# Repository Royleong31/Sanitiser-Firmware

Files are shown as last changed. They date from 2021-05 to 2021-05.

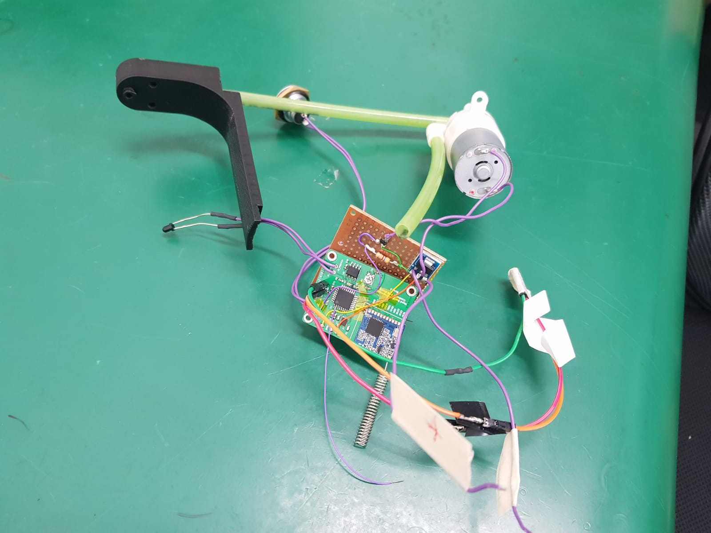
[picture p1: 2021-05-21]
Dispenser without WiFi/Dispenser/Electronics.jpeg

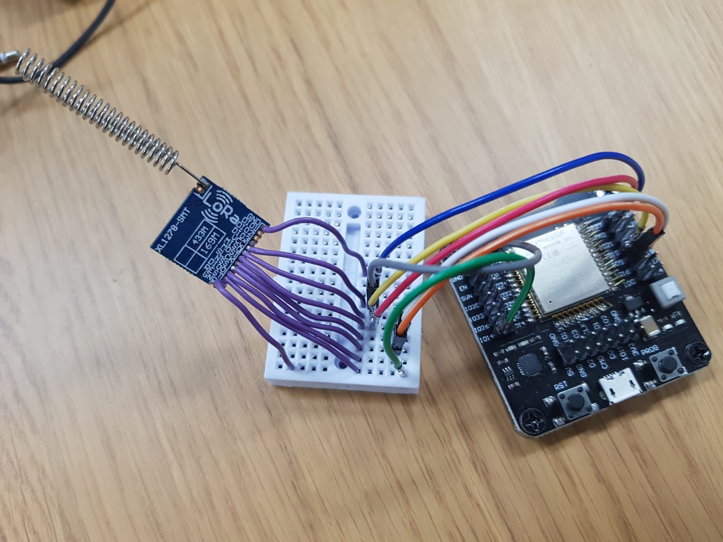
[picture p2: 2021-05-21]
Dispenser without WiFi/Gateway/Gateway Prototype.jpeg

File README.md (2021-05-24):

## General Info about Hand Sanitiser System
- The purpose is to solve the problem of cleaning staff not knowing when the refills of their hand sanitiser dispensers are running out.
- This system aims to alert the users when their dispensers are running out.
- The app will send alert notifications to users to alert them (more information about the hand sanitiser can be found in the hand sanitiser app folder README)
- The app and the firmware for the dispensers and gateway are connected by the Hand Sanitiser backend (more info can be found in that folder)
- There are 2 versions of this system: 
    1) Dispenser with WiFi (this requires the dispenser to be connected to WiFi and plugged into a power supply)
    2) Dispenser without WiFi (this requires the gateway to be connected to WiFi and power supply, but the dispenser is battery operated and does not require a WiFi connection, but not more than 50-100m away from gateway)
- The buffers in the Gateway and Dispenser with WiFi function as circular queues, with the data to be sent being queued (added to the queue). When the data is sent by the API successfully, the data is dequeued (removed from the queue)
- Queues are a form of data structure that follow the First In First Out principle

---------------------------------------------------------------------------------
Bill of materials
- Some components may need to be replaced or added
- If you have any questions regarding the electronics, you can approach Yu Jing

---------------------------------------------------------------------------------

Dispenser without WiFi
- The gateway and dispenser communicate via LoRa, a long range radio protocol.
- Packets are only sent from the dispenser to the gateway (dispenser functions as a beacon, beaming information to the gateway, but the gateway does not reply)
- There are 2 files inside this folder (Gateway and Dispenser)
- LoRa packet is a string, consisting of 3 segments of information, each separated by a space. The first segment is the companyId, second segment is the dispenserId, third is the type of usage.

1) Dispenser
    - A voltage of 3.3V-3.6V is used as that is the required voltage for the MOSFET to work properly (MOSFET is unreliable when GPIO voltage is too low).
    - The dispenser is programmed using an FTDI adapter that is connected to the RX, TX, DTR pins of the PCB. While programming the chip, the chip needs to be powered by the 3.3V and ground of the FTDI.
    
    ~ Electronics
    - Uses a custom PCB with ATMEGA328P chip, runs on 4 AA batteries
    - The input voltage (6V) is converted to 3.3V-3.6V via a DC-DC converter or a LDO regulator 
    - A voltage of 3.3V-3.6V is used as that is the required voltage for the MOSFET to work properly (MOSFET is unreliable when GPIO voltage is too low).
    - The DC-DC converter or LDO will output 3.3V-3.6V into the chip and LoRa module. The maximum GPIO voltage of the chip to be the same as the input voltage of the chip
    - Battery level indicator:
        - 2x500k Ohm resistors form a potential divider circuit between the input power source from the 4x AA batteries and ground.
        - The junction in between the 2 resistors is connected to an analog pin of the ATMEGA. This allows the ATMEGA to measure the input voltage of the batteries. Using a voltage drop curve of AA batteries, the remaining battery life of the batteries can be calculated. 
        - Approximate battery voltages at different battery levels
            - 0%: 3.4V
            - 25%: 4.32V
            - 50%: 4.72V
            - 75%: 5.2V
            - 100%: 6V

    - IR sensor:
        - IR led: Connected to resistor (~3500 Ohms)  in series to ground and the 3.3V-3.6V supply from the DC-DC converter
        - IR phototransistor: Connected to a high resistance (~300k Ohms) pull up resistor. Voltage in between resistor and phototransistor is connected to an analog pin of the ATMEGA as well as a pin on the comparator
    - Motor pins:
        - Positive end is connected to the AA batteries
        - Negative end is connected to the drain of the MOSFET
    - MOSFET pins: 
        - Gate is connected to GPIO pin of ATMEGA. Gate needs to be pulled low to ground.
        - Drain is connected to the negative pin of the motor
        - Source is connected to ground
    - LoRa module
        - The RST, NSS, MOSI, MISO pins go to the corresponding pins on the LoRa module.
    
    ~ Dispensing procedure
    - When hand is placed below the IR sensor, the voltage across the IR phototransistor will vary. This produces an analog voltage signal that is converted to a digital signal by the comparator.
    - A 500k ohm potentiometer is connected to the comparator to produce a reference voltage which the incoming voltage of the IR phototransistor will compare to. A low signal will be produced if the voltage is lower than the reference voltage, signalling that a hand was detected by the IR sensor.
    - The low signal from the comparator will go to interrupt pin 1 of ATMEGA chip, waking it up from deep sleep and dispensing hand sanitiser and send the LoRa packet before going back to sleep.
    - LoRa packet: companyId + ' ' + dispenserId + ' ' + 'usage'
    - In order to dispense hand sanitiser, the motorPin of the ATMEGA chip will be on for about 150ms, this turns on the MOSFET that is connected to the motor. 
    - After dispensing, the ATMEGA chip will go back to sleep
    
    ~ Resetting procedure
    - When the reset button is pressed, a low signal will be sent to pin 0 of the ATMEGA chip, waking it up.
    - The chip will then send 2 LoRa packets to the gateway, informing it that the dispenser has been reset.
    - LoRa packet: companyId + ' ' + dispenserId + ' ' + 'reset'
    - When the button is released, the chip will go back to sleep.

    ~ Battery reading
    - As a 50% potential divider is used (junction is in between 2 500k Ohm resistors), the reading will be half of the raw voltage. 
    - Formula: 
        - Raw battery voltage = analogReading/1023 * (input voltage to ATMEGA) * 2
        - input voltage to ATMEGA is the input voltage to the ATMEGA from the DC-DC converter (usually abt 3.5V). This forms the reference voltage of the chip. 
        - Voltage of the junction in between the 2 potentiometers is half of the actual voltage, thus, you will need to multiply the voltage by 2 to get the actual voltage across the batteries
    
 2) Gateway
    - The gateway uses an ESP32 board as the microcontroller
    - It consists only of an ESP32 connected to a LoRa module.
    - Connected via a USB cable to a wall socket to power the gateway
    - ESP32 has 2 cores. In my code, both cores are running simultaneously, with 1 core handling the receiving of LoRa packets and the other core handling the sending of APIs to the server.
    - Both cores need to be used as the API takes about 2-4s to complete and this can block code execution as Arduino code runs synchronously. By splitting the different tasks into different cores, the ESP32 can both receive packets and send APIs concurrently
    
    ~ Upon receiving a LoRa packet 
    - Store the company ID, dispenser ID and type of usage (usage/reset) into the buffer, which is a 2D array.
    - Position of the counter is stored in a variable, and will increase every time a new packet is received
    
    ~ Procedure of sending APIs to the server
    - Using the company ID, dispenser ID and type of usage, an API is sent to the server to update it that the dispenser has been used/reset.
    - If the API fails, the chip will attempt to send 3 more times before giving up and moving on to the next packet.
    - If the API request is successful, the element in the array will be cleared, allowing data to be written into the same spot.
    
---------------------------------------------------------------------------------

Dispenser with WiFi
- Uses ESP32 board
- The dispenser will be connected to WiFi and plugged into a wall power supply.
- Both of the cores on the ESP32 are used simultaneously, 1 for detecting hand near the IR sensor and another for sending APIs to the server.
- It is similar to the system without WiFi, just without the LoRa part. 
- There is no PCB yet, just an ESP32, resistors, MOSFET, IR led, IR phototransistor and motor mounted on a donut board.
- As the dispenser and company IDs are unique to the dispenser, the buffer array is only 1 dimensional, instead of 2 dimensional like in the gateway above. (dispenserId and companyId are stored as global variables in the code)

~ Upon detecting a hand
- The string 'usage' will be inserted into the buffer array. 
- The counter that stores the position of the next available slot in the buffer will increase.

~ Upon reset button being pressed
- The string 'reset' will be inserted into the buffer array. 
- The counter that stores the position of the next available slot in the buffer will increase.

~ Procedure of sending APIs to the server
- When there is a packet of data to be sent, the API will send the data with the companyId, dispenserId and the type of usage.
- API counter, which stores the position of the data of the last sent API, will increase.

---------------------------------------------------------------------------------
Potential Improvements
- The battery life of the hand sanitiser dispenser could be improved. The battery consumption of the chip is only about 0.15mA, however, the IR sensor consumes a significant amount of power (up to 4mA) as it is always on. The best way to improve battery life is to reduce the power consumption of the IR led.
- There is often packet loss or packet corruption when data is transfered from the dispenser to the gateway, resulting in inaccurate data. This could be improved by implementing a handshake algorithm between dispenser an gateway in order to ensure that messages are reliably transfered. 
- The old PCB that I am using works, but there are a couple of errors regarding the IR sensor as the designer forgot to include it. Therefore, I have ordered a new one. 
- Alerts can be sent to users when the battery is running out. When the battery is running low, the dispenser can send a LoRa packet to the gateway to update the database.
- A PCB should be made for the dispenser with WiFi. All the components and ESP32 chip can be put directly on the PCB.

-----------------------------------------------------------------------------------
Summary
- Active IR sensors have 2 components: the IR led and IR phototransistor. IR led is always on as it is the IR emitter. The IR phototransistor is the IR receiver. So when a hand is placed near the sensor, IR light from the IR led will bounce off the hand and reach the IR phototransistor. This causes the resistance of the IR phototransistor to drop, leading to a drop in potential difference, which can be read by a comparator or analog pin of ATMEGA.

- Dispenser with WiFi: 
    - Detecting Hand: IR sensor read by analog in => add data to buffer
    - Reset button pressed: Button press detected by digital pin => add data to buffer
    - When data in buffer: Send API request => if successful => clear data from buffer
    - This system is more reliable as it is much simpler than the one without wifi

- Dispenser without WiFi
    - Dispenser: 
        - Detecting Hand: IR sensor reading read by comparator => wake up chip => chip sends LoRa packet => chip goes back to sleep
        - Reset Button pressed: Change is detected by wake up pin => Chip wakes up => chip sends 2 LoRa packets => chip goes back to sleep
        - Battery level indicator: Raw voltage of battery with potential divider => analog pin => calculate raw voltage => use the raw voltage of battery to determin battery life
    - Gateway:
        - Receiving data: Stores data in 2D array buffer
        - Sending data: Reads data from buffer and sends API => if successful => clear data from buffer

-----------------------------------------------------------------------------------
Things that you need to do
- Understand how the system works together
- Use the new PCB that Yu Jing designed, and integrate the battery level indicator feature (for dispenser without wifi), which is not yet in the code.
- You will need to manually calibrate the 500k trim pot with a screwdriver
- Build the casing for the gateway and dispensers. Aaron has designed the casing for the dispenser with wifi and Vaishakh designed the casing for dispenser without wifi. You need to liaise with them and ensure that the casing fits the PCB and all the customer requirements.
- It's important to improve the power consumption of the IR sensor (for dispenser without wifi). The power consumption of the rest of the components is more or less good enough. The biggest problem is the IR sensor, specifically the IR led.
- All the best!!!

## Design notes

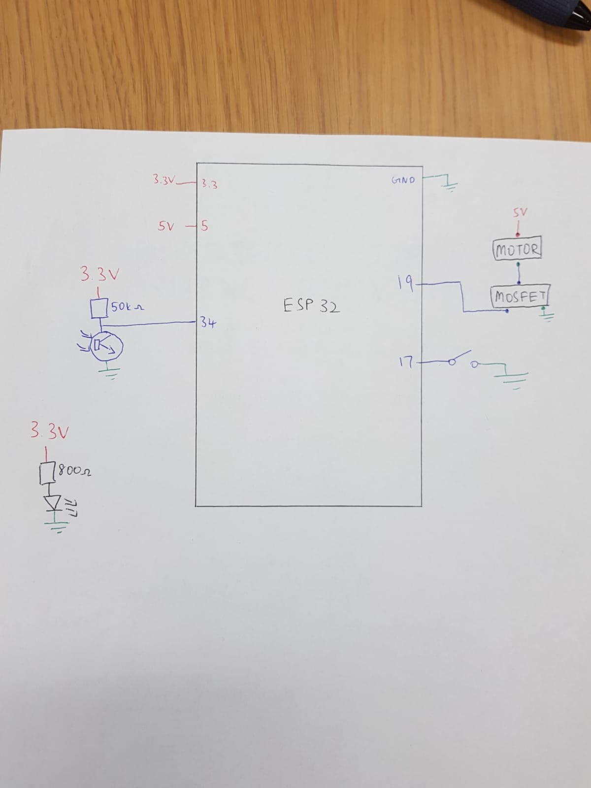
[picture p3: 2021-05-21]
Dispenser with WiFi/Schematic.jpeg

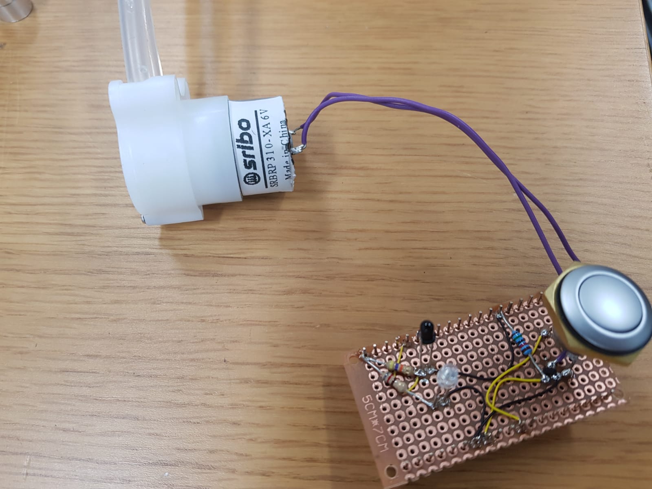
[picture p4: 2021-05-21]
Dispenser with WiFi/Prototype.jpeg

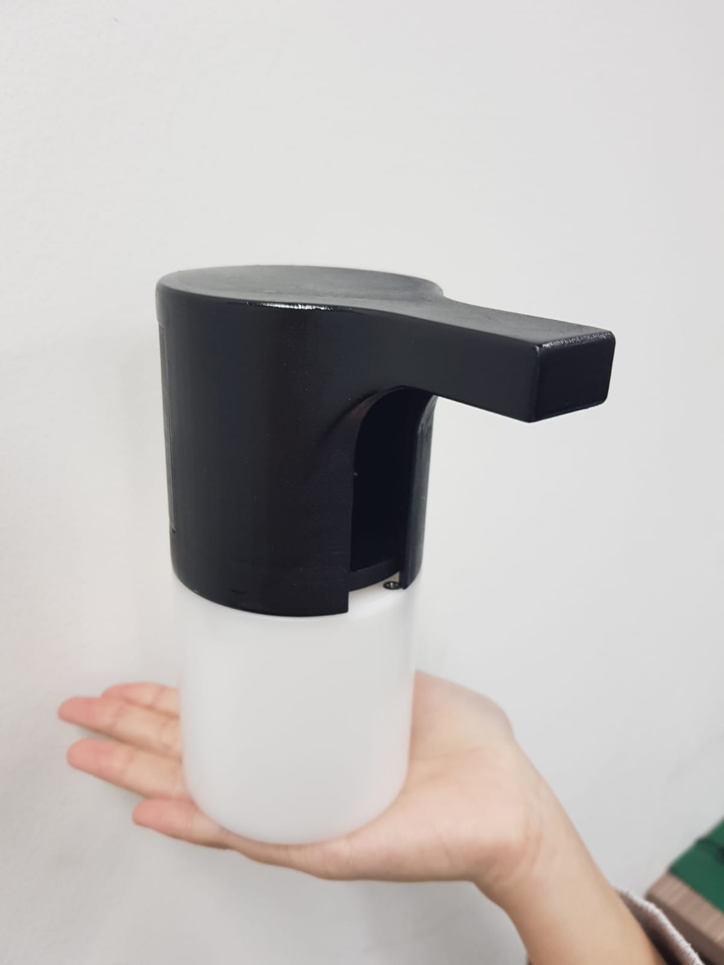
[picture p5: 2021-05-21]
Dispenser without WiFi/Dispenser/Dispenser Prototype.jpeg

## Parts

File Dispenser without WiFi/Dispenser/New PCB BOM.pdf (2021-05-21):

Revised: Tuesday, May 18, 2021 Revision:

Bill Of Materials | May 21,2021 | 17:59:23 Page1
Item | Quantity Reference Part
______________________________________________

1 7 C1,C2,C6,C8,C9,C10,C11 100nF
2 | 1 C3 | 10nF
3 | 2 C4,C5 | 22pF
4 | 1 C7 | 47uF
5 | 1 D1 | LED
6 | 1 R1 | 22K
7 | 1 R2 | 330K
8 | 1 R3 | 1K
9 3 R4,R5,R7 500K
10 | 1 R6 | 3.5K
11 | 1 T1 | MECH-RESET
12 | 2 T2,T8 | GND
13 | 1 T3 | RX
14 | 1 T4 | TX
15 | 1 T5 | DTR
16 | 1 T6 | IR-PHOTO+
17 | 1 T7 | IR-PHOTO-
18 | 1 T9 | VOUT
19 | 1 T10 | VIN
20 | 1 U1 | ATMEGA328P-AU
21 | 1 U2 | SO8
22 | 1 X2 | 16MHz

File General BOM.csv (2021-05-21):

Quantity | Manufacturer | Manufacturer Part Number | Note
2 | AVX Corporation | 0603YA220KAT2A | CAP CER 22PF 16V NP0 0603
7 | KEMET | C0603C104Z3VACTU | CAP CER 0.1UF 25V Y5V 0603
1 | Samsung Electro-Mechanics | CL10X106MO8NRNC | 10µF ±20% 16V Ceramic Capacitor X6S 0603 (1608 Metric)
1 | Murata Electronics | GRM188R60J476ME15D | CAP CER 47UF 6.3V X5R 0603
1 | Bourns Inc. | TC33X-2-504E | TRIMMER 500K OHM 0.1W J LEAD TOP
1 | Yageo | RC0603FR-07330KL | RES SMD 330K OHM 1% 1/10W 0603
1 | Yageo | AC0603JR-0722KL | RES SMD 22K OHM 5% 1/10W 0603
1 | Stackpole Electronics Inc | RMCF0603JJ1K00 | RES 1K OHM 5% 1/10W 0603
1 | MICROCHIP TECH | ATMEGA328-AU | Buy from: https://www.digipart.com/part/ATMEGA328-AU
1 | STMicroelectronics | TS393CDT | IC COMPARATOR DUAL MCRPWR 8-SOIC
1 | Kyocera International Inc. Electronic Components | CX3225GB16000D0HPQCC | 16MHz ±20ppm Crystal 8pF 80 Ohms 4-SMD
1 | Vishay Dale | D55342H07B4B50RWS | 4.5k Ohm Resistor
 | https://www.alibaba.com/product-detail/310-Mini-Peristaltic-Small-Electric-Water_1600059520516.html |  | Alternate motor
1 | https://www.aliexpress.com/item/4001286693357.html?spm=a2g0s.9042311.0.0.9ebd4c4d33xxlZ |  | Motor
1 | Vishay Dale | CRCW0805400KJNTA | 400k Ohm Resistor
1 | https://www.aliexpress.com/item/32910242359.html |  | SX1278 LoRa Module
1 | Infineon Technologies | IRLML2803TRPBF | N-channel MOSFET
1 | Casing |  | Need to manufacture ourselves
1 | ourpcb.com |  | Printed Circuit Board: Already have 1 design but may need to change design
1 | https://shopee.sg/50pairs-3mm-940nm-LEDs-infrared-emitter-and-IR-receiver-diodes-EACH-50PCS-i.56539845.1525606581 |  | IR led (3mm)
1 |  |  | IR Phototransistor (3mm)
0.2m | Silicone 0.6mm piping
1 | Omron Electronics | B3F-1020 | Button
1 | Microchip | MCP1825ST-3302E/DB | Low Dropout Voltage Regulator
1 | Need to source for 1 |  | DC-DC converter (~6V to 3.5V)
1 |  |  | 4x AA battery holder
Hand Sanitiser Gateway
Name | Quantity
SX1278 LoRa Module | 1 | same as the LoRa module above
ESP32 | 1
Casing | 1

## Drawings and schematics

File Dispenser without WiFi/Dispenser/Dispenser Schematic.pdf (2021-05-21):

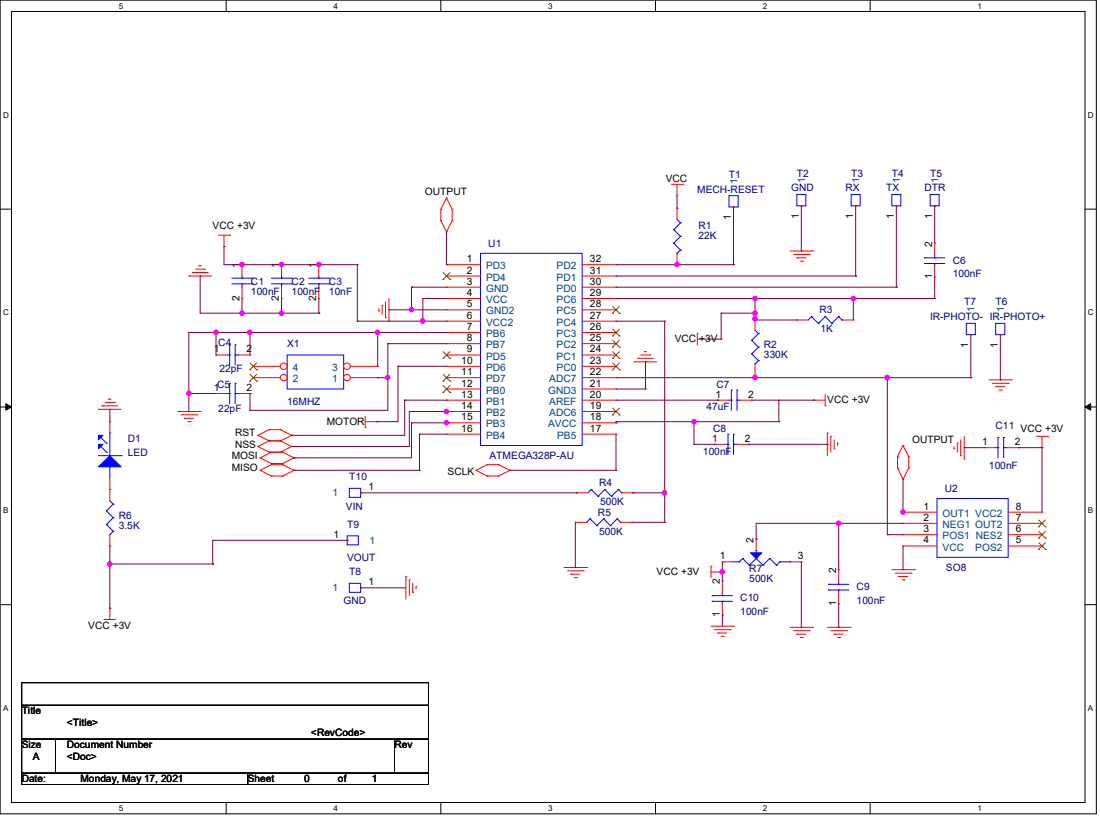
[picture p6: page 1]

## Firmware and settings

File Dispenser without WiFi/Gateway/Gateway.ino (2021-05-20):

#include <SPI.h>
#include <LoRa.h>
#include <WiFi.h> 
#include <HTTPClient.h>
#include <ArduinoJson.h>

//define the pins used by the transceiver module        FOR ESP32 ONLY
#define ss 5
#define rst 14
#define dio0 2
 
// Insert WiFi name and password
const char* ssid = "";
const char* password = "";

// 2D array that stores LoRa packets from dispensers
// Each 'row' (the one with [1000]) stores the information from each packet
// Each 'column' (the one with [3]) stores the information from each packet
// As each packet has 3 types of information (companyId, dispenserId, typeOfUsage), this allows the system to store data from 1000 packets
// The buffer functions as a queue, with incoming requests starting from the back of the queue
String buffer[1000][3];

// APIcounter stores the position of the current API request
int APIcounter = 0;

// packetCounter stores the position of the spot that will be used for the incoming LoRa packet
int packetCounter = 0;

// APIcounter will 'follow' packetCounter as the packetCounter adds data into the buffer(as data is received from dispensers) and APIcounter removes data from the buffer(as API requests are made successfully)

TaskHandle_t Task1;
TaskHandle_t Task2;

  // Restarts the counter when the counter reaches the end of the queue
void resetBuffer() {
  buffer[APIcounter][0] = buffer[APIcounter][1] = buffer[APIcounter][2] = "";

  if (APIcounter < 999) {
    APIcounter++;
  } else {
    APIcounter = 0;
  }
}

void setup() {
  //initialize Serial Monitor
  Serial.begin(9600);
  while (!Serial);
  Serial.println("LoRa Receiver");
 
  //setup LoRa transceiver module       FOR ESP32 ONLY
  LoRa.setPins(ss, rst, dio0);
  
  while (!LoRa.begin(433E6)) {
    Serial.println(".");
    (500);
  }

  // Setting the spreading factor and coding rate of LoRa helps to increase the range (look at <LoRa.h> library docs on github for more details)
  LoRa.setSpreadingFactor(12);
  LoRa.setCodingRate4(8);

  Serial.println("LoRa Initializing OK!");

  WiFi.begin(ssid, password);

  while (WiFi.status() != WL_CONNECTED) {
    delay(500);
    Serial.println("Connecting to WiFi..");
  }
 
  Serial.println("Connected to the WiFi network");

  //create a task that will be executed in the Task1code() function, with priority 1 and executed on core 0
  xTaskCreatePinnedToCore(
                    Task1code, 
                    "Task1",
                    10000,      
                    NULL,      
                    1,          
                    &Task1,      
                    0);                   
  delay(500); 

  //create a task that will be executed in the Task2code() function, with priority 1 and executed on core 1
  xTaskCreatePinnedToCore(
                    Task2code,   
                    "Task2",     
                    10000,       
                    NULL,        
                    1,           
                    &Task2,      
                    1);          
    delay(500); 
}



void Task1code( void * pvParameters ){
  // Details are similar to the Dispenser with WiFi file
  int numOfTimesTried = 0;
  while (true) {
   if (WiFi.status() == WL_CONNECTED) {
      if (buffer[APIcounter][0] != "" && numOfTimesTried < 4) {
        Serial.println("Starting api send");
        const int apiStart = millis();
        HTTPClient client;
        char jsonOutput[128];
        String userId = buffer[APIcounter][0];
        String dispenserId = buffer[APIcounter][1];
        String typeOfUsage = buffer[APIcounter][2];

        if (typeOfUsage == "usage") {
          client.begin("https://us-central1-hand-sanitiser-c33d1.cloudfunctions.net/usage/" + userId + '/' + dispenserId + "/usage");
        } else if (typeOfUsage == "reset") {
          client.begin("https://us-central1-hand-sanitiser-c33d1.cloudfunctions.net/usage/" + userId + '/' + dispenserId + "/reset");
        }
   
        int httpCode = client.PATCH(jsonOutput);
         Serial.println("Time that posting API needs to execute: " + String(millis() - apiStart));
        
        if (httpCode == 200) {
          String payload = client.getString();
          Serial.println("\nStatuscode: " + String(httpCode));
          Serial.println(payload);
          client.end();

          resetBuffer();
          
        } else {
          numOfTimesTried++;
          Serial.println("Error on HTTP request");
          Serial.println("Error Code " + String(httpCode));
        } 
      } else if (numOfTimesTried >= 4) {
        numOfTimesTried = 0;
        resetBuffer();
      }
    }
    
    else {
        Serial.println("Connection lost"); 
        WiFi.disconnect();
        WiFi.begin(ssid, password);
        delay(3000);
       if (WiFi.status() == WL_CONNECTED) {
        Serial.println("Device reconnected to WiFi");
       }
       }
      delay(100);
    } 
  } 

void Task2code( void * pvParameters ){
  while (true) {
    // Variables to store the data from incoming LoRa packets
    String LoRaData;
    // Array of 3 strings as the LoRa packet has 3 types of info (companyId, dispenserId, typeOfUsage)
    String currentPacketData[3] = {"", "", ""};

    //try to parse packet
    int packetSize = LoRa.parsePacket();
    if (packetSize) {
      //received a packet
      Serial.print("Received packet ");
  
      //read packet
      while (LoRa.available()) {
        // add the LoraData to the buffer array
        LoRaData = LoRa.readString();
        Serial.print(LoRaData);
      }
  
      //print RSSI of packet
      int rssi = LoRa.packetRssi();
      Serial.print(" with RSSI ");
      Serial.println(rssi);

      int arrayCounter = 0;
      
      for (int i=0; i<LoRaData.length(); i++) {
        // Write the data into the currentPacketData array        
        if (LoRaData[i] != ' ') {
          currentPacketData[arrayCounter] += LoRaData[i];

        // Each component in the LoRaData is separated by a space(' '), so this helps to seperate the data into the 3 elements in currentPacketData
        } else {
          arrayCounter++;
        }
      }

      // Prints out the data from the incoming packet
      for (int i=0; i<3; i++) {
        Serial.print(currentPacketData[i]);
        Serial.println("|");
      }
  
  //    ADD THE DATA TO THE BUFFER
      if (buffer[packetCounter][0] == "") {
        buffer[packetCounter][0] = currentPacketData[0];      // companyId
        buffer[packetCounter][1] = currentPacketData[1];      // dispenserId
        buffer[packetCounter][2] = currentPacketData[2];      // usage/reset
      }

      // Restarts the counter when the counter reaches the end of the queue
      if (packetCounter < 999) {
        packetCounter++;
      } else {
        packetCounter = 0;
      }
    }
  }
}

void loop() {
   vTaskDelete(NULL);
}

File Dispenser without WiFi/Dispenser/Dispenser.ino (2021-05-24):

/* 
The chip sleeps by default in order to save power. There are 2 interrupt pins, pin 1 and pin 0 on the chip, which are used to wake the chip up.
Pin 1 is used by the IR sensor, and will interrupt the chip when it is low. 
- A comparator is used to convert the analog signal from the IR phototransistor to a digital signal, which is then used to wake the chip up.

Pin 0 is used by the button. A pull down resistor is attached to the button in order to wake up the chip when the button is pressed. 
- Button pressed -> pin 0 is pulled low -> chip wakes up
*/


#include <avr/sleep.h>
#include <SPI.h>
#include <LoRa.h>

const int motorPin = 6;
const int buttonPin = 2;
const int unitNum = 1;

const String companyId = "Fj7JOWRl8OFoUKNPzLPU";
const String dispenserId = "23456789";

void setup()
{
  // put your setup code here, to run once:
  Serial.begin(9600);
  Serial.println("setting up");
  pinMode(3, INPUT_PULLUP);
  pinMode(2, INPUT);
  pinMode(6, OUTPUT);

  // Frequency of the LoRa module is 433MHz
  if (!LoRa.begin(433E6))
  { 
    Serial.println("Starting LoRa failed!");
    while (1);
  }

  // Needs to match the settings on the gateway
  LoRa.setSpreadingFactor(12);
  LoRa.setTxPower(20);
  LoRa.setCodingRate4(8);
}

void loop() {
  sleepFunction();
}

void sleepFunction()
{
  sleep_enable();
  LoRa.sleep();

  set_sleep_mode(SLEEP_MODE_PWR_DOWN);

  // attach the interrupt on int0
  attachInterrupt(1, interruptFunction, LOW); // IR sensor to detect hand
  attachInterrupt(0, buttonInterrupt, LOW);   // Button to detect reset

  sleep_cpu();
  Serial.println("Woke up!");
}

// Dispensing hand sanitiser function
void interruptFunction()
{
  Serial.println("Hand detected!"); //A7 is the ir transistor

  // turn on the motor
  digitalWrite(motorPin, HIGH);

  // I used a for loop to create a delay as the chip's Real Time Clock(RTC) is put to sleep so delay() does not work.
  for (int i=0; i < 120; i++) {
    Serial.println(i);
  }
  digitalWrite(motorPin, LOW);

  Serial.println("Sending dispenser info");

  // Sending the LoRa packet to the gateway 
  // Packet Structure: companyId + ' ' + dispenserId + ' ' + "usage"/"reset"
  LoRa.beginPacket();
  LoRa.print(companyId);
  LoRa.print(" ");
  LoRa.print(dispenserId);
  LoRa.print(" ");
  LoRa.print("usage");
  LoRa.endPacket();
  Serial.println("Sent dispenser info");

  Serial.println(analogRead(A7));

  // White the hand is too near, run through the while loop so that the hand sanitiser will not be dispensed twice.
  while (analogRead(A7) > 900)
  {
    Serial.println("Hand is too near");
    Serial.println(analogRead(A7));
  }
  Serial.println("Going to sleep");

  // Put the chip back to sleep after dispensing
  sleep_disable();
  detachInterrupt(1);
  LoRa.sleep();
}

// Button pressed to reset function
void buttonInterrupt()
{
  Serial.println("Button was pressed!");
  Serial.println("Sending reset packet 1");
  Serial.println("Sending reset packet 2");

    // 2 packets are sent to gateway when resetting in order to increase the chance that the gateway will receive the packet (minimise risk of packet loss)
    LoRa.beginPacket();
    LoRa.print(companyId);
    LoRa.print(" ");
    LoRa.print(dispenserId);
    LoRa.print(" ");
    LoRa.print("reset");
    LoRa.endPacket();  
    for (int i=0; i < 50; i++) {
      Serial.println(i);
    }
    LoRa.beginPacket();
    LoRa.print(companyId);
    LoRa.print(" ");
    LoRa.print(dispenserId);
    LoRa.print(" ");
    LoRa.print("reset");
    LoRa.endPacket(); 

  Serial.println("Finished sending reset packet");

  // While button is pressed, don't do anything else
  while (digitalRead(2) == 0) {}

  // Put the chip back to sleep 
  sleep_disable();
  detachInterrupt(0);
  LoRa.sleep();
}

// Add this to the code to get the battery level
// <inputVoltage> is the voltage to chip from DC-DC converter
// analog pin A4 is connected to the potential divider that the raw battery voltage is connected to
// 1023 is used as ATMEGA reads analog readings in 10 bit resolution, so from 0 to 1023
//  Times 2 to get actual battery voltage
// float batteryLevel = analogRead(A4) / 1023 * <inputVoltage> * 2;
